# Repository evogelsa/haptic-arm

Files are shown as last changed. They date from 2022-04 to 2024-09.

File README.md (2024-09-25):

# Haptic Arm

## Overview

This repository contains all the code and files related to the SCARA haptic arm
I built while working as an undergraduate researcher. The arm is a 2DOF
"revolute-revolute" robot. What makes this project special is the control
methods used on the arm. A combination of inverse and forward kinematics are
used to carefully apply forces to the end-effector depending on the current arm
configuration. These forces are determined by a vector field that maps out the
desired magnitudes and directions for points on a cartesian plane.

A simulation of the arm using this code can be seen here (hint: click the image
to see it animated).

Simulation (https://i.imgur.com/62qTkmU.webm)

### File Descriptions

The files in this repository are as follows.

```txt
├── cad
│   └── assembly.stp                --> 3D CAD files to replicate design
├── LICENSE.md                      --> MIT license this project is under
├── pics
│   ├── arm_base.jpg                --> Picture of the ARM base assembly
│   └── odrive.jpg                  --> Picture of the ODrive on the arm base
├── README.md                       --> This file
├── references.md                   --> Some references I found useful
└── src
    ├── calculate.py                --> Helper functions and classes for math
    ├── condition-number-heatmap
    │   └── condition_number.png    --> Heat map of condition number for arm
    ├── device.py                   --> Hardware interface classes and methods
    ├── font
    │   └── Inconsolata-Regular.ttf --> Font file for visualization
    ├── lib
    │   ├── libfreetype-6.dll       --> DLL required for running vis on Windows
    │   ├── SDL2.dll                --> DLL required for running vis on Windows
    │   ├── SDL2_ttf.dll            --> DLL required for running vis on Windows
    │   └── zlib1.dll               --> DLL required for running vis on Windows
    ├── main.py                     --> Runs haptic simulation on the robot
    ├── pyproject.toml              --> Rules for formatting with Black
    ├── requirements.txt            --> Project requirements
    ├── theta-heatmap
    │   ├── circle_dtheta0.png      --> Heat map of motor 0 vel for circle VF
    │   ├── circle_dtheta1.png      --> Heat map of motor 1 vel for circle VF
    │   ├── circle_theta0.png       --> Heat map of motor 0 pos for circle VF
    │   ├── circle_theta1.png       --> Heat map of motor 1 pos for circle VF
    │   ├── spring_dtheta0.png      --> Heat map of motor 0 vel for spring VF
    │   ├── spring_dtheta1.png      --> Heat map of motor 1 vel for spring VF
    │   ├── spring_theta0.png       --> Heat map of motor l pos for spring VF
    │   └── spring_theta1.png       --> Heat map of motor 1 pos for spring VF
    └── visualize.py                --> Visualization and simulation for program
```

## Design

### Software

The code takes a class based approach to just about everything. The
`HapticDevice` class is the primary interface to the hardware and wraps the
odrive instance as well as methods and parameters to help in calibration and
manipulation of the device. The `VectorField` class defines the various
vector fields that are responsible for calculating the forces to apply to the
robot. The `Coord` class is a helper class to translate points between cartesian
coordinates (x and y in meters) to polar coordinates (r and theta also in
meters) and to "window" coordinates (matrix like i and j in pixels). Finally all
of the classes in `visualize.py` are used for rendering out the visualization
and simulation of the arm, but are not essential for robot operation.

### Hardware

The current robot design uses 3D printed arms with timing pulleys. The motors
are stacked at the base of the robot, and they manipulate the arms through
timing belts. Motor control is done through a 24V ODrive motor controller
(hardware v3.5). Two CUI AMT102-V encoders are used in conjunction with two
ODrive D5065-270K motors to drive the robot.

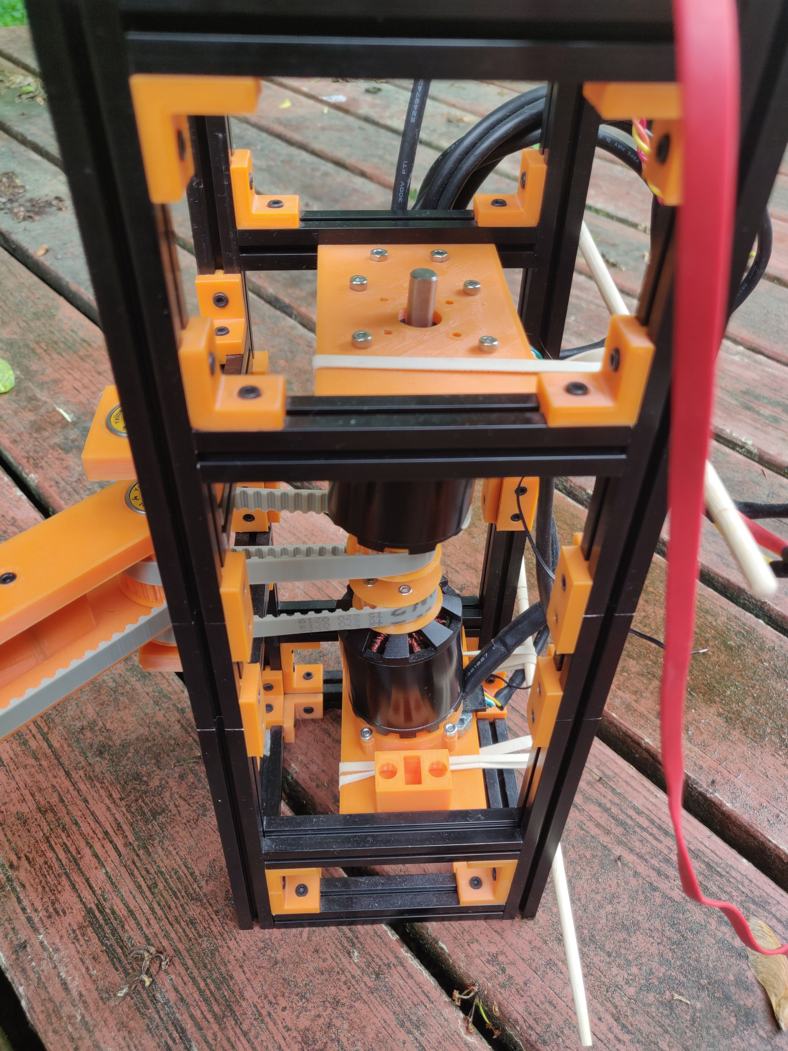
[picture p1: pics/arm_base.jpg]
arm


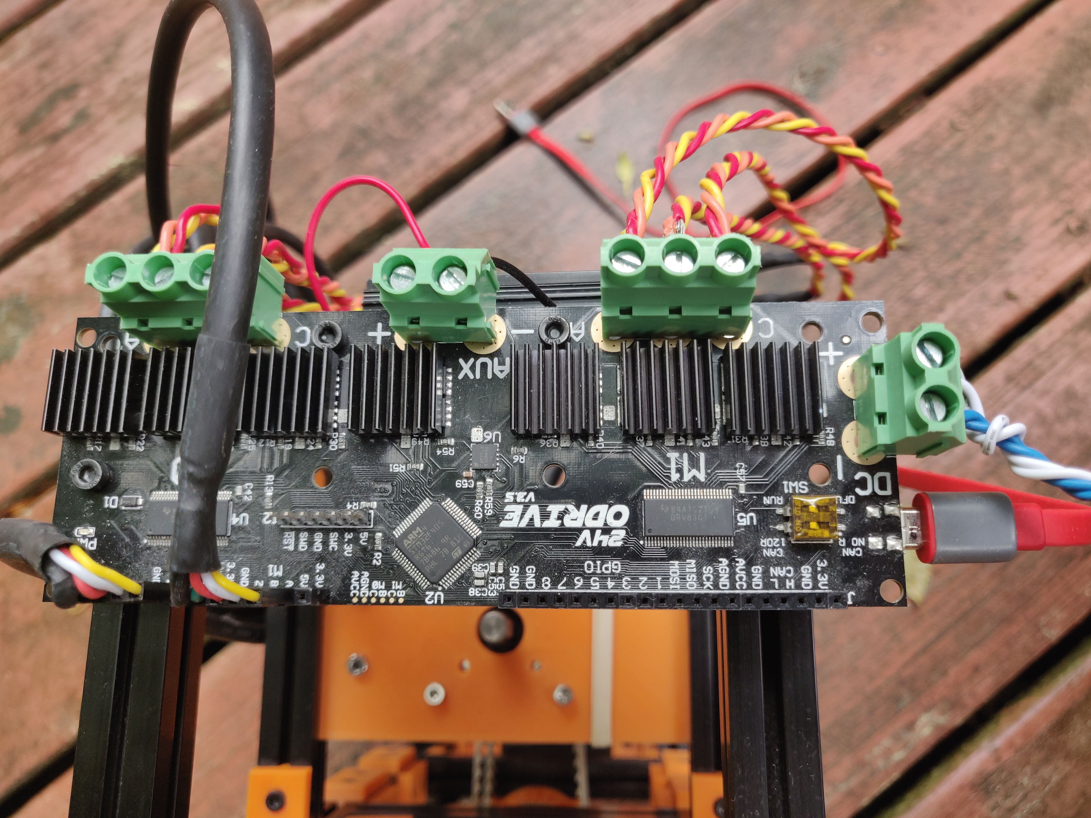
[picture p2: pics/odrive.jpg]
odrive


Mechanical design is not my strong suit, but the upside is that this robot
should be relatively hardware agnostic. A person with more hardware skill and
knowledge should be able to take this project and develop a new design that
applies the same SCARA-like principles and then successfully run the code with
minimal modification. The motor locations and distances should not matter as
long as the arm lengths are adjusted in the `HapticDevice` class instances.

STEP files of the current design are provided in the [cad](cad) folder.
The device is not properly assembled or organized, but all the parts for 3D
printing can be found there.

### Bill of Materials

If you do want to replicate the design I used, here is a rough bill of
materials.

| Part | Part Number | Quantity |
|---|---|---|
| OpenBeam precut kit | 100540 | 1 |
| ODrive (v3.5+) | ODrive v3.5 | 1 |
| ODrive dual shaft motor 270 kV | D5065-270KV | 2 |
| CUI encoders | AMT102-V | 2 |
| Cable for CUI AMT-102 | find on ODrive shop | 2 |
| Yellow Jacket 608 bearings 8 pack | B071DT4V1Q | 2 |
| M8 all thread | xx | 1 meter |
| M8 nuts | xx | 4 |
| Various M3 screws and nuts | xx | 50 or less |
| T5 73 tooth timing belt | T5-365-10 | 1 |
| T5 37 tooth timing belt | T5-185-10 | 2 |

## Setup and Use

### ODrive

The ODrive, motors, and encoders will need to be configured before this project
can be used. Documentation on the
[odrive website](https://docs.odriverobotics.com/) should be followed for this.
Most importantly, the PIDs of the controller will need to be well tuned for the
motors to work effectively.

### Code

All software files and resources are contained in the [src](src) folder. Before
running any code, the python modules listed in the
[requirements](requirementes.txt) should be installed first through pip.

```txt
pip -r requirements.txt
```

If running the visualization on a Windows computer, the DLLs in the
[lib](src/lib) folder will need to be present in the src directory, same as they
are in this repo. If running on linux, SDL2 and SDL2_TTF should be installed
manually or through your package manager. For Arch:

```txt
# pacman -Syu sdl2 sdl2_ttf
```

If already connected to an ODrive, the [main.py](src/main.py) can be run
directly. Some command line arguments are available and can be listed with the
following.

```txt
python3 main.py --help
```

Because the program will start by calibrating the encoders, it is necessary that
the motors are able to rotate freely. For the current hardware design, this
means the timing belts must be disengaged from the motor pulleys during
calibration, hence the purpose of the sliding motor mounts.

If not connected to hardware, or if a simulation is desired,
[visualize.py](src/visualize.py) can also be run as main. The same or similar
command line arguments will be required and can be listed in similar manor.

```txt
python3 visualize.py --help
```

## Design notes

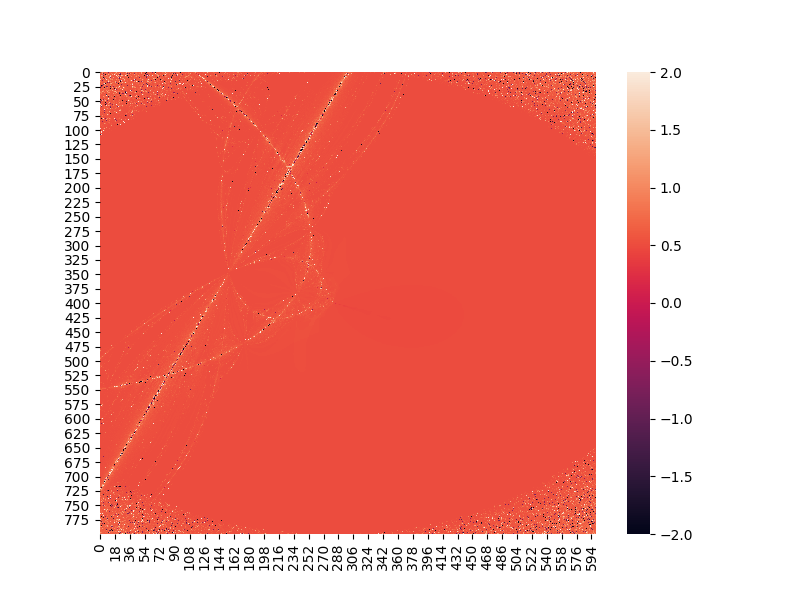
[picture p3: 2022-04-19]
src/theta-heatmap/circle_dtheta1.png

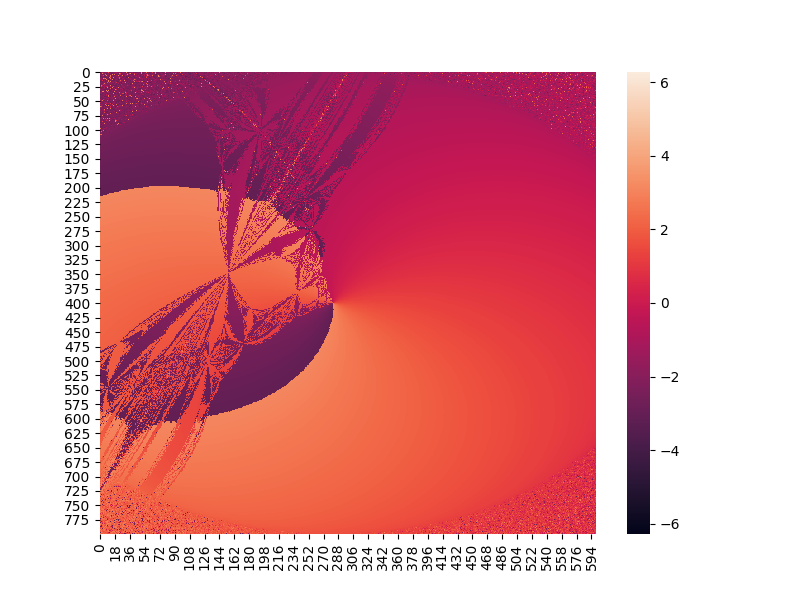
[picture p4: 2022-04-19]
src/theta-heatmap/spring_theta1.png

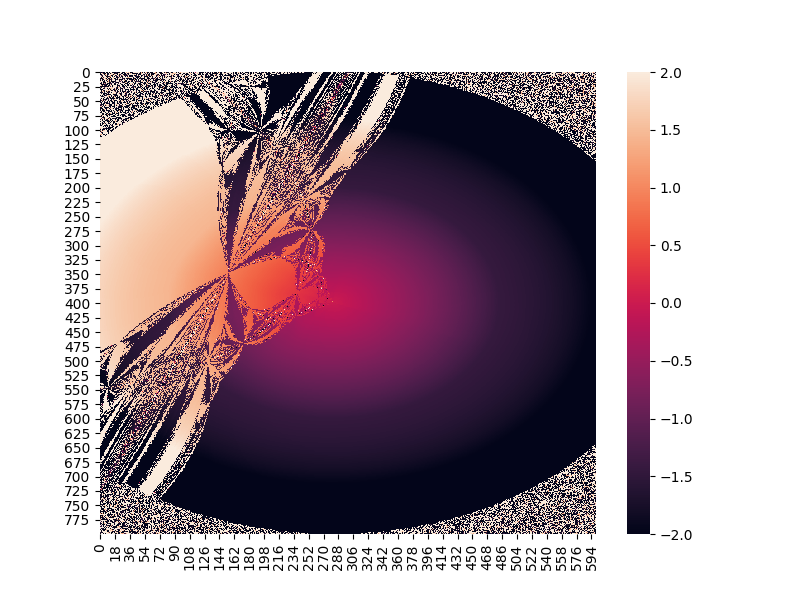
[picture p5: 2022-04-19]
src/theta-heatmap/spring_dtheta0.png

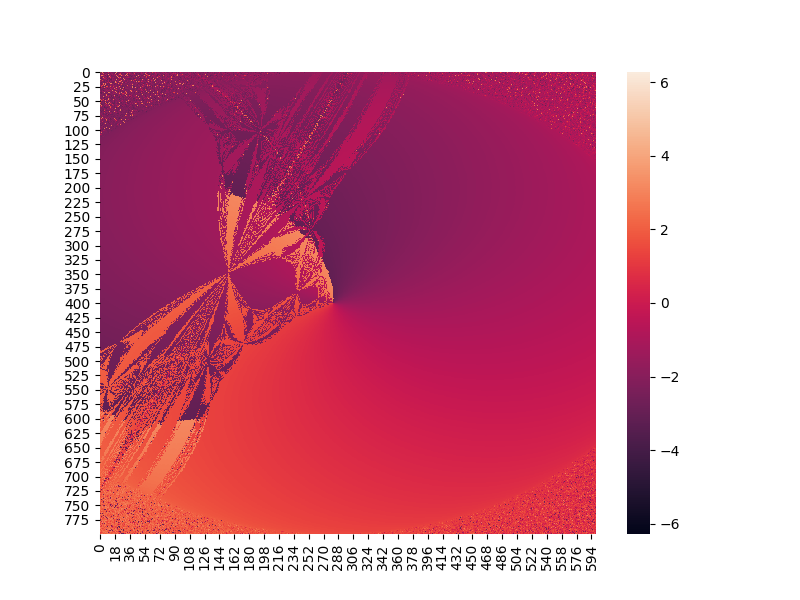
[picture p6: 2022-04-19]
src/theta-heatmap/spring_theta0.png

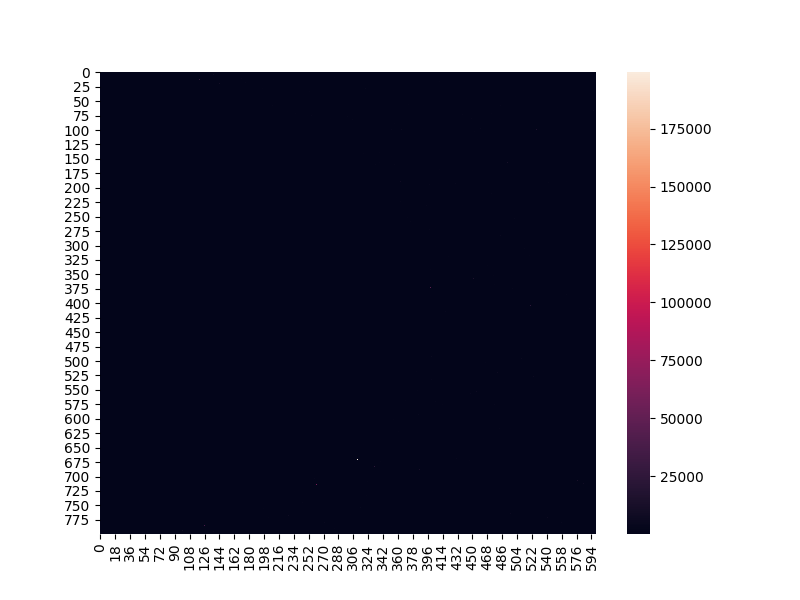
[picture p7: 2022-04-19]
src/condition-number-heatmap/condition_number.png

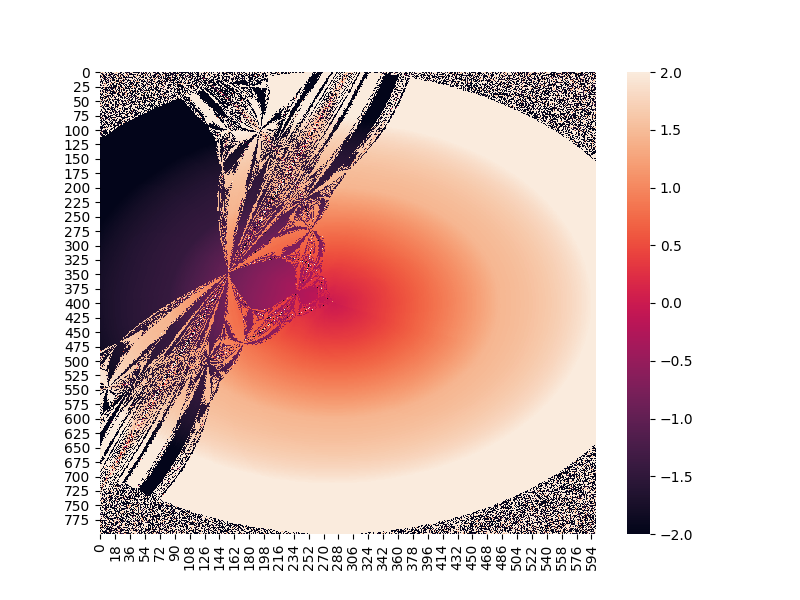
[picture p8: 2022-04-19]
src/theta-heatmap/spring_dtheta1.png

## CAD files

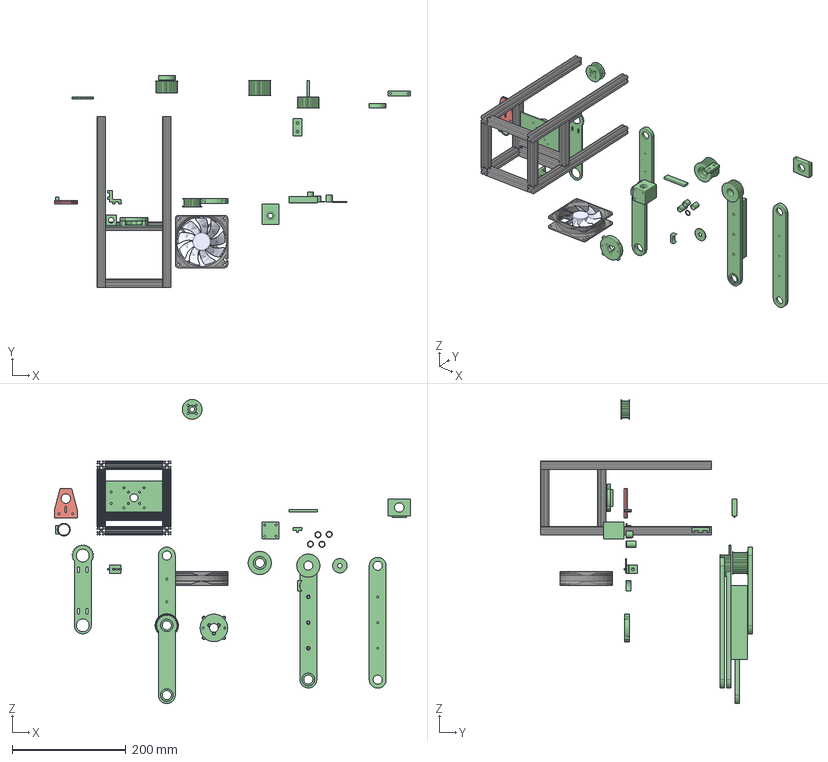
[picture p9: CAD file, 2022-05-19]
cad/assembly.stp
625.2 x 372.5 x 534.2 mm
Openbeam 300 mm v2 x 4
Openbeam/MakerbeamXL 100mm x 8
Right Angle Bracket
MotorPlate v1
EncoderPlate v1
Interface Plate
F9 body
F9 fan
Arm Bottom
Forearm
Pulley Bearing
Arm Top
odrive-motor-mount
motor-pulley
bearing-cap
arm-top
screw-tensioner-v3

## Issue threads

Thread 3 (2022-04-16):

Create a heat map of condition number for the workspace

evogelsa, 2022-04-16:

evogelsa, 2022-05-10:
Added prototype in 366a2f0e0c981ba523768f1493f3e796c8ec235f. Results seem bugged

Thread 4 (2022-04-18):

Fix theta_heatmap

evogelsa, 2022-04-18:
ValueError from `calculate.map` relating to passing an array as parameter for v

evogelsa, 2022-04-19:
b4bd97c fixes the issue for the spring vector field. Other vector fields still have issues since the `VectorField` class was not originally meant to take arrays as parameters. Requires more work to be a total fix.

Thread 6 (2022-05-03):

Improve calibration routine

evogelsa, 2022-05-03:
Rather than requiring calibration at program start each time, store calibration data or automate the calibration routine. This likely would also require design changes to make the arm more constrained and have less slop.

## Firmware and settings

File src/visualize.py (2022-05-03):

import calculate
import device

import collections
import matplotlib.pyplot as plt
import seaborn as sb
import numpy as np
import time
import os
import sys
import argparse

# check for OS and add sdl dlls if on windows
if sys.platform == 'win32':
    sdlpath = os.path.join(os.path.dirname(__file__), 'lib')
    os.environ['PYSDL2_DLL_PATH'] = sdlpath
# include resources
font = os.path.join(os.path.dirname(__file__), 'font/Inconsolata-Regular.ttf')

import sdl2
import sdl2.ext


# define some basic colors
WHITE = sdl2.ext.Color(255, 255, 255)
BLACK = sdl2.ext.Color(0, 0, 0)
RED = sdl2.ext.Color(255, 0, 0)
GREEN = sdl2.ext.Color(0, 255, 0)
BLUE = sdl2.ext.Color(0, 0, 255)
ORANGE = sdl2.ext.Color(232, 90, 9)
CYAN = sdl2.ext.Color(0, 255, 255)

# standard window size
WIN_WIDTH = 800
WIN_HEIGHT = 600

# global state variable used by main to check status of visualization
STATE_RUNNING = False


# Render system to handle rendering texture sprites (the robot)
class TextureRenderSystem(sdl2.ext.TextureSpriteRenderSystem):
    """TextureRenderSystem is a class which converts texures to sdl sprites"""

    def __init__(self, renderer):
        super(TextureRenderSystem, self).__init__(renderer)
        self.renderer = renderer


# arm segment
class ArmSegment(sdl2.ext.Entity):
    """ArmSegment is a class which holds the necessary utility functions and
    graphics for a single arm segment (one rectangle in the visualization)"""

    def __init__(self, world, sprite, wposi=0, wposj=0, angle=0):
        pos = calculate.Coord(
            wpos=(wposi, wposj), win_width=WIN_WIDTH, win_height=WIN_HEIGHT
        )
        self.world = world
        self.sprite = sprite
        self.sprite.pos = pos
        self.sprite.angle = angle
        self.sprite.position = self.get_origin()
        self.sprite.point = sdl2.SDL_Point(int(self.sprite.size[0] / 2), 0)

    def get_origin(self):
        """gets the top left corner of segment for sdl rect in window cords"""
        cornerx = int(self.sprite.pos.window.j - self.sprite.size[0] / 2)
        cornery = self.sprite.pos.window.i
        return cornerx, cornery

    def get_end(self):
        """gets the middle of the end of segment in polar cords"""
        ox, oy = self.sprite.pos.cartesian
        x = (self.sprite.size[1] / calculate.PIXELS_PER_METER) * np.cos(
            np.radians(-self.sprite.angle)
        ) + ox
        y = (self.sprite.size[1] / calculate.PIXELS_PER_METER) * np.sin(
            np.radians(-self.sprite.angle)
        ) + oy
        end = calculate.Coord(
            cpos=(x, y), win_width=WIN_WIDTH, win_height=WIN_HEIGHT
        )
        return end.polar.r, end.polar.theta

    def get_config(self):
        """returns the equivalent joint angle of the arm segment"""
        return np.radians(-self.sprite.angle)

    def update(self, wposj, wposi, angle):
        """Sets the position and angle of the segment on the window to the
        given window coordinates and angle"""
        self.sprite.pos.window = (wposi, wposj)
        self.sprite.angle = angle

    def draw(self, spriterenderer):
        """Creates the sprite on the given renderer"""
        cornerx, cornery = self.get_origin()
        r = sdl2.SDL_Rect(
            cornerx, cornery, self.sprite.size[0], self.sprite.size[1]
        )
        p = self.sprite.point
        sdl2.SDL_RenderCopyEx(
            spriterenderer.sdlrenderer,
            self.sprite.texture,
            None,
            r,
            self.sprite.angle,
            p,
            0,
        )


class SDLWrapper:
    """SDLWrapper holds together all the basic SDL systems and other classes
    which help in producing the graphics"""

    def __init__(
        self,
        window=None,
        renderer=None,
        fontmanager=None,
        spritefactory=None,
        world=None,
        spriterenderer=None,
        tracelen=500,
    ):
        self.window = window
        self.renderer = renderer
        self.fontmanager = fontmanager
        self.spritefactory = spritefactory
        self.world = world
        self.spriterenderer = spriterenderer
        self.trace = tracelen > 0

        # set by self.text
        self.text_sprites = None

        # set by self.vector_stream_plot
        self.vectors = None
        self.squares = None
        self.center = None

        # calculated inside of self.step
        self.config_buffer = collections.deque([])
        self.trace_buffer = collections.deque(maxlen=tracelen)

        # set by self.arm_workspace
        self.workspace_points = None

        # set by self.generate_device
        self.arms = None

        # init sdl systems
        sdl2.ext.init()

        # create window, renderer, and the factory to create sprites
        if self.window is None:
            self.window = sdl2.ext.Window(
                "Haptic Device", size=(WIN_WIDTH, WIN_HEIGHT)
            )
        if self.renderer is None:
            self.renderer = sdl2.ext.Renderer(self.window)
        if self.fontmanager is None:
            self.fontmanager = sdl2.ext.FontManager(font)
        if self.spritefactory is None:
            self.spritefactory = sdl2.ext.SpriteFactory(
                sdl2.ext.TEXTURE,
                renderer=self.renderer,
                fontmanager=self.fontmanager,
            )

        if self.world is None:
            # create world
            self.world = sdl2.ext.World()

        if self.spriterenderer is None:
            # create sprite renderer with the texture system
            self.spriterenderer = TextureRenderSystem(self.renderer)

        # add sprite renderer to world
        self.world.add_system(self.spriterenderer)

        # make the window visible and start simulation loop
        self.window.show()

    def text(self, text: list, size=16):
        """Takes a list of lists and converts the contents into lines of text
        placed at the bottom left of the window"""
        start_height = WIN_HEIGHT - size * len(text)
        start_width = 0
        text_sprites = []
        for i in range(len(text)):
            for j in range(len(text[i])):
                text_sprites.append(
                    self.spritefactory.from_text(
                        text[i][j], size=size, color=BLACK, bg_color=WHITE
                    )
                )
                text_sprites[-1].position = (start_width, start_height)
                start_width += text_sprites[-1].size[0] + 16
                if start_width > WIN_WIDTH:
                    print(i, j, text)
                    raise Exception('Line too long to fit on window')
            start_height += size
            start_width = 0
        self.text_sprites = text_sprites

    def vector_stream_plot(self, vf):
        """Visualizes the given vector field with a stream plot. Small
        rectangles mark the sampling points and the trails move in the direction
        of the vector field at those sampled points. Green rect shows the center
        of the vector field."""
        center = calculate.Coord(
            cpos=(vf.args['xcenter'], vf.args['ycenter']),
            win_width=WIN_WIDTH,
            win_height=WIN_HEIGHT,
        )

        self.vectors = []  # stores points of vector lines
        self.squares = []  # stores sampled points
        self.center = [center.window.j - 5, center.window.i - 5, 10, 10]

        # step size defines how much space between each sample point in number
        # of pixels
        step_size = 40
        # iterate over the width and height of the window, includes bounds if
        # step_size is a multiple of height and width
        for y in np.arange(
            0, WIN_HEIGHT // step_size * step_size + 1, step_size
        ):
            for x in np.arange(
                0, WIN_WIDTH // step_size * step_size + 1, step_size
            ):
                # add initial point to squares and start a vector line
                vector = []
                coord = calculate.Coord(
                    wpos=(y, x), win_width=WIN_WIDTH, win_height=WIN_HEIGHT
                )
                vector.extend((int(coord.window.j), int(coord.window.i)))
                self.squares.append((x - 3, y - 3, 6, 6))
                # sample n points in direction of vf from origin and add to the
                # list of vectors
                for _ in range(20):
                    dx, dy = vf.return_vectors(*coord.cartesian)
                    dx /= 50
                    dy /= 50
                    coord.cartesian = (
                        coord.cartesian.x + dx,
                        coord.cartesian.y + dy,
                    )
                    vector.extend((int(coord.window.j), int(coord.window.i)))
                self.vectors.append(vector)

    @staticmethod
    def theta_heatmap(arm, vf):
        """
        Create and update a texture that is a single color channel heatmap
        representing the theta velocities.
        """
        # TODO heatmap for theta velocities
        # [x] calculate ik
        # [x] write method to impl newton-raphson (numerical ik)
        # [x] click on point in space and it calcs config and draws arm
        # [ ] for range of theta0 and theta1 calc jacobian and ratio of
        #     eigenvalues of jacobian, smaller eigenvalue / bigger eigenvalue

        #  print('analytical:', arm.inv_kinematics(0, 0.4))
        #  print('numerical:', arm.inv_kinematics_num(0, 0.4))

        binsz = 1
        num_samples = WIN_WIDTH * WIN_HEIGHT // (binsz ** 2)

        imat, jmat = np.meshgrid(
            np.arange(0, WIN_HEIGHT, binsz), np.arange(0, WIN_WIDTH, binsz)
        )
        imat = imat.flatten()
        jmat = jmat.flatten()

        xmat, ymat = calculate.Coord(
            wpos=(imat, jmat), win_width=WIN_WIDTH, win_height=WIN_HEIGHT
        ).cartesian

        dxmat, dymat = vf.return_vectors(xmat, ymat)

        if not os.path.isdir('theta-heatmap'):
            os.mkdir('theta-heatmap')

        if os.path.isfile(f'theta-heatmap/{vf.field}_data.npz'):
            data = np.load(f'theta-heatmap/{vf.field}_data.npz')
            dthetamatrix0 = data['dthetamatrix0']
            dthetamatrix1 = data['dthetamatrix1']
            th0mat = data['Th0']
            th1mat = data['Th1']
        else:
            th0mat = np.empty(num_samples)
            th1mat = np.empty(num_samples)
            for idx, (x, y) in enumerate(zip(xmat, ymat)):
                theta0, theta1 = arm.inv_kinematics_num(x, y)
                th0mat[idx] = theta0
                th1mat[idx] = theta1
                print(f'Calculating IK: {idx+1}/{num_samples}', end='\r')
            print()

            dthetamatrix0 = np.empty(num_samples)
            dthetamatrix1 = np.empty(num_samples)
            for idx, (t0, t1, dx, dy) in enumerate(
                zip(th0mat, th1mat, dxmat, dymat)
            ):
                dthetas = arm.inv_jacobian(t0, t1) @ np.array([dx, dy])
                dthetamatrix0[idx] = dthetas[0]
                dthetamatrix1[idx] = dthetas[1]
                print(f'Calculating ijac: {idx+1}/{num_samples}', end='\r')
            print()

            print('Saving data...', end='\r')
            np.savez_compressed(
                f'theta-heatmap/{vf.field}_data',
                Th0=th0mat,
                Th1=th1mat,
                dthetamatrix0=dthetamatrix0,
                dthetamatrix1=dthetamatrix1,
            )
            print('Saving data...done')

        print('Generating dtheta0 heatmap...', end='\r')
        plt.figure(figsize=(WIN_WIDTH / 100, WIN_HEIGHT / 100))
        sb.heatmap(
            dthetamatrix0.reshape((WIN_WIDTH // binsz, WIN_HEIGHT // binsz)),
            vmin=-2,
            vmax=2,
        )
        #  cbar=False, xticklabels=False, yticklabels=False)
        plt.savefig(f'theta-heatmap/{vf.field}_dtheta0.png')
        print('Generating dtheta0 heatmap...done')

        print('Generating theta0 heatmap...', end='\r')
        plt.figure(figsize=(WIN_WIDTH / 100, WIN_HEIGHT / 100))
        sb.heatmap(
            th0mat.reshape((WIN_WIDTH // binsz, WIN_HEIGHT // binsz)),
            vmin=-2 * np.pi,
            vmax=2 * np.pi,
        )
        #  cbar=False, xticklabels=False, yticklabels=False)
        plt.savefig(f'theta-heatmap/{vf.field}_theta0.png')
        print('Generating theta0 heatmap...done')

        print('Generating dtheta1 heatmap...', end='\r')
        plt.figure(figsize=(WIN_WIDTH / 100, WIN_HEIGHT / 100))
        sb.heatmap(
            dthetamatrix1.reshape((WIN_WIDTH // binsz, WIN_HEIGHT // binsz)),
            vmin=-2,
            vmax=2,
        )
        #  cbar=False, xticklabels=False, yticklabels=False)
        plt.savefig(f'theta-heatmap/{vf.field}_dtheta1.png')
        print('Generating dtheta1 heatmap...done')

        print('Generating theta1 heatmap...', end='\r')
        plt.figure(figsize=(WIN_WIDTH / 100, WIN_HEIGHT / 100))
        sb.heatmap(
            th1mat.reshape((WIN_WIDTH // binsz, WIN_HEIGHT // binsz)),
            vmin=-2 * np.pi,
            vmax=2 * np.pi,
        )
        #  cbar=False, xticklabels=False, yticklabels=False)
        plt.savefig(f'theta-heatmap/{vf.field}_theta1.png')
        print('Generating theta1 heatmap...done')

    @staticmethod
    def condition_number_heatmap(arm):
        """
        Generates a heat map of the condition number
        """
        binsz = 1
        num_samples = WIN_WIDTH * WIN_HEIGHT // (binsz ** 2)

        imat, jmat = np.meshgrid(
            np.arange(0, WIN_HEIGHT, binsz), np.arange(0, WIN_WIDTH, binsz)
        )
        imat = imat.flatten()
        jmat = jmat.flatten()

        xmat, ymat = calculate.Coord(
            wpos=(imat, jmat), win_width=WIN_WIDTH, win_height=WIN_HEIGHT
        ).cartesian

        if not os.path.isdir('condition-number-heatmap'):
            os.mkdir('condition-number-heatmap')

        if os.path.isfile(f'condition-number-heatmap/data.npz'):
            data = np.load(f'condition-number-heatmap/data.npz')
            kmat = data['kmat']
        else:
            th0mat = np.empty(num_samples)
            th1mat = np.empty(num_samples)
            for idx, (x, y) in enumerate(zip(xmat, ymat)):
                theta0, theta1 = arm.inv_kinematics_num(x, y)
                th0mat[idx] = theta0
                th1mat[idx] = theta1
                print(f'Calculating IK: {idx+1}/{num_samples}', end='\r')
            print()

            kmat = np.empty(num_samples)
            for idx, (th0, th1) in enumerate(zip(th0mat, th1mat)):
                k = arm.condition_number(th0, th1)
                kmat[idx] = k
                print(
                    f'Calculating condition numbers: {idx+1}/{num_samples}',
                    end='\r',
                )
            print()

            print('Saving data...', end='\r')
            np.savez_compressed(
                f'condition-number-heatmap/data',
                kmat=kmat,
            )
            print('Saving data...done')

        print('Generating condition number heatmap...', end='\r')
        plt.figure(figsize=(WIN_WIDTH / 100, WIN_HEIGHT / 100))
        sb.heatmap(
            kmat.reshape((WIN_WIDTH // binsz, WIN_HEIGHT // binsz)),
        )
        plt.savefig(f'condition-number-heatmap/condition_number.png')
        print('Generating condition number heatmap...done')

    def arm_workspace(self, arm: device.HapticDevice):
        points = []

        t1 = 5 * np.pi / 6
        for t0 in np.linspace(np.pi / 2, -np.pi / 2, num=1000):
            x, y = arm.fwd_kinematics(t0, t0 + t1)
            c = calculate.Coord(
                cpos=(x, y), win_width=WIN_WIDTH, win_height=WIN_HEIGHT
            )
            points.extend((int(c.j), int(c.i)))

        t0 = -np.pi / 2
        for t1 in np.linspace(5 * np.pi / 6, 0, num=1000):
            x, y = arm.fwd_kinematics(t0, t0 + t1)
            c = calculate.Coord(
                cpos=(x, y), win_width=WIN_WIDTH, win_height=WIN_HEIGHT
            )
            points.extend((int(c.j), int(c.i)))

        t1 = 0
        for t0 in np.linspace(-np.pi / 2, np.pi / 2, num=1000):
            x, y = arm.fwd_kinematics(t0, t0 + t1)
            c = calculate.Coord(
                cpos=(x, y), win_width=WIN_WIDTH, win_height=WIN_HEIGHT
            )
            points.extend((int(c.j), int(c.i)))

        self.workspace_points = points

    def generate_device(self, arm=device.HapticDevice(init_with_device=False)):
        """Generate device takes the haptic device class and turns it into two
        arm segments that will represent the arm"""
        arm0_sprite = self.spritefactory.from_color(
            BLUE, size=(30, int(arm.arm0.length * calculate.PIXELS_PER_METER))
        )
        arm0 = ArmSegment(
            self.world, arm0_sprite, wposj=WIN_WIDTH // 2, wposi=0, angle=0
        )

        endr, endtheta = arm0.get_end()
        pos = calculate.Coord(
            ppos=(endr, endtheta), win_width=WIN_WIDTH, win_height=WIN_HEIGHT
        )
        arm1_sprite = self.spritefactory.from_color(
            ORANGE, size=(30, int(arm.arm1.length * calculate.PIXELS_PER_METER))
        )
        arm1 = ArmSegment(
            self.world,
            arm1_sprite,
            wposj=pos.window.j,
            wposi=pos.window.i,
            angle=0,
        )
        self.arms = (arm0, arm1)

    def update_device(self, theta0, theta1):
        """Updates the device configuration with the given angles"""
        pos = self.arms[0].sprite.pos
        angle0 = np.degrees(-theta0)  # pi - theta0
        self.arms[0].update(pos.window.j, pos.window.i, angle0)

        r, theta = self.arms[0].get_end()
        pos = calculate.Coord(
            ppos=(r, theta), win_width=WIN_WIDTH, win_height=WIN_HEIGHT
        )
        angle1 = np.degrees(-theta1)
        self.arms[1].update(pos.window.j, pos.window.i, angle1)

    def smooth_move_to_location(self, arm, x, y, resolution=0.001):
        if len(self.config_buffer) > 0:
            thetas = self.config_buffer[-1]
        else:
            thetas = [arm.get_config() for arm in self.arms]

        p = arm.fwd_kinematics(*thetas)
        pd = np.array([x, y])

        v = np.array([x, y]) - np.array(p)
        vhat = v / np.linalg.norm(v)

        num_ik = arm.inv_kinematics_num(*pd)
        an_ik = arm.inv_kinematics(*pd)
        #  print(f'num ik: {num_ik} | ana ik: {an_ik}')

        while np.linalg.norm(pd - (p := resolution * vhat + p)) > resolution:
            thetas = arm.inv_kinematics_num(*p)
            self.config_buffer.append(thetas)

    # run simulation
    def step(self) -> float:
        """Advances the visualization one time/sim step ahead"""
        # time frame start
        frame_start = time.monotonic()

        # clear old graphics and update state for next frame
        self.renderer.clear()

        if self.vectors is not None:
            for vector in self.vectors:
                self.renderer.draw_line(vector, color=WHITE)
            self.renderer.draw_rect(self.squares, color=WHITE)
            self.renderer.fill(self.center, color=GREEN)

        # render traces
        if self.trace:
            p = calculate.Coord(
                ppos=self.arms[1].get_end(),
                win_width=WIN_WIDTH,
                win_height=WIN_HEIGHT,
            )
            self.trace_buffer.append((int(p.j - 2), int(p.i - 2), 4, 4))
            self.renderer.fill(self.trace_buffer, color=RED)

        if self.workspace_points:
            self.renderer.draw_line(self.workspace_points, color=CYAN)

        # render arm sprites
        for arm in self.arms:
            arm.draw(self.spriterenderer)

        # render text sprites onto window
        if self.text_sprites:
            self.spriterenderer.render(self.text_sprites)

        self.renderer.present()

        # preserve physics by calculating elapsed time and delaying if necessary
        # to limit to only 60 FPS. This prevents the robot velocity being
        # dependent on the frame rate of the simulation
        elapsed_time = time.monotonic() - frame_start
        if elapsed_time < 1 / 60:
            sdl2.SDL_Delay(int((1 / 60 * 1000) - (elapsed_time * 1000)))
            elapsed_time = time.monotonic() - frame_start

        return elapsed_time
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

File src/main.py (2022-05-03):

import device
import calculate
import visualize

from argparse import ArgumentParser
import numpy as np


MAX_VEL0 = 4
MAX_VEL1 = 4


def step(arm, vf, vis=None):
    # get current arm configuration
    theta0, theta1 = arm.get_config()

    # get position of end effector with kinematic equations [units of meters]
    x, y = arm.fwd_kinematics(theta0, theta1)

    # get desired vectors from defined vector field [units of meters/s]
    dx, dy = vf.return_vectors(x, y)

    # create matrix of vectors
    vectors = np.array([dx, dy])

    # calculate angular velocities with inv jacobian and matrix multiplication
    # [units of rad/s]
    ijac = arm.inv_jacobian(theta0, theta1)
    thetas = ijac @ vectors
    dtheta0, dtheta1 = thetas

    # convert rad/s to counts/s
    dcount0 = arm.rad2count(dtheta0, 0)
    dcount1 = arm.rad2count(dtheta1, 1)

    # convert counts/s to turns/s
    vel0 = dcount0 / arm.odrive.axis0.encoder.config.cpr
    vel1 = dcount1 / arm.odrive.axis1.encoder.config.cpr

    # limit velocities to set maximums to avoid overspeed errors
    vel0 = min(vel0, MAX_VEL0)
    vel1 = min(vel1, MAX_VEL1)
    vel0 = max(vel0, -MAX_VEL0)
    vel1 = max(vel1, -MAX_VEL1)

    arm.odrive.axis0.controller.input_vel = vel0
    #  arm.odrive.axis0.controller.input_torque = vel0

    arm.odrive.axis1.controller.input_vel = vel1
    #  arm.odrive.axis1.controller.input_torque = vel1

    if vis is not None:
        count0 = arm.rad2count(theta0, 0)
        count1 = arm.rad2count(theta1, 1)
        line1 = "count0 : {:9.0f} | count1 : {:9.0f}".format(count0, count1)
        line2 = "theta0 : {:9.2f} | theta1 : {:9.2f}".format(theta0, theta1)
        line3 = "x      : {:9.2f} | y      : {:9.2f}".format(x, y)
        line4 = "dx     : {:9.2f} | dy     : {:9.2f}".format(dx, dy)
        line5 = "dtheta0: {:9.2f} | dtheta1: {:9.2f}".format(dtheta0, dtheta1)
        line6 = "dcount0: {:9.2f} | dcount1: {:9.2f}".format(dcount0, dcount1)
        line7 = "vel0   : {:9.2f} | vel1   : {:9.2f}".format(vel0, vel1)
        paragraph = [
            [line1],
            [line2],
            [line3],
            [line4],
            [line5],
            [line6],
            [line7],
        ]
        vis.text(paragraph, size=16)
        vis.update_device(theta0, theta1)
        vis.step()


def stop(arm):
    try:
        arm.restart()
    except:
        print('Device restarted')


def main():
    # instantiate a haptic device (connects to odrive)
    arm = device.HapticDevice()

    # redefine max velocities
    global MAX_VEL0, MAX_VEL1
    MAX_VEL0 = arm.odrive.axis0.controller.config.vel_limit / 4
    MAX_VEL1 = arm.odrive.axis1.controller.config.vel_limit / 4

    # calibrate encoders with odrive calibration routine
    arm.odrive.axis0.clear_errors()
    arm.odrive.axis1.clear_errors()
    arm.calibrate()

    # use custom homing routine to define counts/angle
    arm.home()

    input('Press enter to continue...')

    # setup control mode
    arm.set_ctrl_mode_velocity()

    # parse cl arguments
    parser = ArgumentParser(description='Parse field parameters')
    parser.add_argument(
        '-xc',
        '--xcenter',
        dest='xcenter',
        type=float,
        default=np.sqrt(2) * arm.arm0.length,
        help='center of vector field in x direction',
    )
    parser.add_argument(
        '-yc',
        '--ycenter',
        dest='ycenter',
        type=float,
        default=0,
        help='center of vector field in y direction',
    )
    parser.add_argument(
        '-dt',
        '--dtheta',
        dest='dtheta',
        type=float,
        default=0.5,
        help='rotational speed of vector field',
    )
    parser.add_argument(
        '-r',
        '--radius',
        dest='radius',
        type=float,
        default=arm.arm0.length / 4,
        help='radius from field center for deadband',
    )
    parser.add_argument(
        '-b',
        '--buffer',
        dest='buffer',
        type=float,
        default=arm.arm0.length / 4 * 0.05,
        help='size of deadband',
    )
    parser.add_argument(
        '-dr',
        '--drmax',
        dest='drmax',
        type=float,
        default=0.5,
        help='the max radial speed towards center of field',
    )
    parser.add_argument(
        '-f',
        '--field',
        dest='field',
        type=str,
        default='spiralbound',
        help='field type: circle, circlebound, spiral, '
        + 'spiralbound, spring',
    )
    args = parser.parse_args()

    # instantiate vector field for arm
    vf_args = {
        'xcenter': args.xcenter,
        'ycenter': args.ycenter,
        'dtheta': args.dtheta,
        'radius': args.radius,
        'buffer': args.buffer,
        'drmax': args.drmax,
    }
    field = args.field
    vf = calculate.VectorField(arm, field=field, args=vf_args)

    # create visualization window
    vis = visualize.SDLWrapper()
    # and generate the arm segments
    vis.generate_device(arm)
    # and draw the vector field
    vis.vector_stream_plot(vf)

    print('Press Ctrl + C to exit, or close the visualization window')

    try:
        visualize.STATE_RUNNING = True
        while visualize.STATE_RUNNING:
            step(arm, vf, vis)
        stop(arm)
    except KeyboardInterrupt:
        stop(arm)


if __name__ == "__main__":
    main()

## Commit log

2019-03-20 added odrive files
2019-03-21 moved odrive into dir
2019-04-24 tested & fixed accel, savgol filter accel plt
2019-08-06 Set motor torque with amp input
2019-11-05 add arm class
2019-11-05 update couple errors
2019-11-06 fixed wps, todo pid tune
2020-07-04 modify for new motor testing
2020-07-04 port go arm simulation to python
2020-08-14 begin integration of simulation and arm control
2020-08-22 add link to simulation from physical arm
2020-08-22 rename folder to indicate simulation controlling arm
2020-10-16 fix python bugs and change to vel control
    [calculate.py, main.py]
2020-10-17 fix axes and change homing
    [device.py, main.py, visualize.py]
2020-11-11 fix vis and control bug, set torque ctrl
    [calculate.py, device.py, main.py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]
2021-02-03 add fix for spring field
    [calculate.py]
2021-03-01 switch back to velocity mode
2021-04-05 add calculate methods to device and update heatmap
2021-04-05 update heatmap methods to use arrays
2021-04-06 add test changes to remove areas outside workspace
    May have fixed out of bounds error for arccos, but ideally only want to
    calculate this heatmap for values that are inside the workspace to lower
    perf cost and avoid any other errors. Need to get update texture working
    so the workspace can be plot just as solid colors to test its working.
    [calculate.py, device.py, visualize.py]
2021-04-28 fix stream plot rotation and ad click ik
    [device.py, visualize.py]
2022-04-16 cast trace coords to int, add CYAN
2022-04-19 partial fixes for #4
    still errors on fields other than spring
    [calculate.py, visualize.py]
2022-04-19 add condition number and fixes for #4
    fixed issue with variable name in theta hm
    condition number heatmap performs simialr to theta
    [device.py, visualize.py]
2022-05-17 add bom
2022-05-17 add timing belts
2022-05-19 restructure directories and complete #7
    [assembly.stp]
